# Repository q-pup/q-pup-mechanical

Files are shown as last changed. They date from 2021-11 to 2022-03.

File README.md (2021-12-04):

# q-pup-mechanical
CAD Models and Mechanical Design Calculations for Q-PUP

## McMaster-Carr Part Links
### Motor Module
- Cycloidal disk bearing: https://www.mcmaster.com/5972K341/ (x2)
- Cycloidal drive input/output bearing: https://www.mcmaster.com/5972K91/ (x2)
- Cycloidal drive pin bushings: https://www.mcmaster.com/6294K444/ (x8)
- Output hub bearing: https://www.mcmaster.com/5972K248/ (x1)

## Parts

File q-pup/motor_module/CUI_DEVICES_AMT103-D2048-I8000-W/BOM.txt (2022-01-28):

3DX_CUI_DEVICES_Supplier: CUI Devices
3DX_CUI_DEVICES_Description: AMT10 Axial, Adjustable Resolution, 2048 PPR, Single Index Pulse, 8 mm Bore, Wide, Incremental, Capacitive Modular Encoder
3DX_CUI_DEVICES_Model Number: AMT103-D2048-I8000-W

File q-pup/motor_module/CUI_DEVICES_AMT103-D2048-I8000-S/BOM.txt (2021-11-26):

3DX_CUI_DEVICES_Supplier: CUI Devices
3DX_CUI_DEVICES_Description: AMT10 Axial, Adjustable Resolution, 2048 PPR, Single Index Pulse, 8 mm Bore, Standard, Incremental, Capacitive Modular Encoder
3DX_CUI_DEVICES_Model Number: AMT103-D2048-I8000-S

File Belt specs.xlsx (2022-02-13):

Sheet: Sheet1
 | power [kW] | speed [RPM] | Torque [Nm] | Pulley dia [mm] | Force [N] | Belt Width [mm] | Tensile Strength per belt width [N/mm]
Req | 0.42 | 30.00 | 133.33 | 160.00 | 1666.67 |  |  | 103.2258065
Omega HP | 5.00 | 2850.00 | 16.75 | 76.39 | 438.60 | 9.00 | 48.73
 | 0.10 | 10.00 | 95.49 | 81.49 | 2343.55 | 20.00 | 117.18
 | 0.19 | 20.00 | 90.71 | 81.49 | 2226.37 | 20.00 | 111.32 | 1.328012435
 | 0.28 | 30.00 | 90.18 | 81.49 | 2213.35 | 20.00 | 110.67
 | 0.47 | 50.00 | 89.76 | 81.49 | 2202.94 | 20.00 | 110.15
 | 1.71 | 200.00 | 81.64 | 81.49 | 2003.74 | 20.00 | 100.19
 | 20.00 | 3000.00 | 63.66 | 81.49 | 1562.37 | 20.00 | 78.12
 | 43.92 | 8000.00 | 52.42 | 81.49 | 1286.61 | 20.00 | 64.33
DELTA | 0.22 | 20.00 | 105.04 | 81.49 | 2577.91 | 12.00 | 214.83
 | 0.32 | 30.00 | 100.26 | 81.49 | 2460.73 | 12.00 | 205.06 | 4101.214873 | 1.842105263
 | 0.41 | 40.00 | 97.88 | 81.49 | 2402.14 | 12.00 | 200.18

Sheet: Pulley Design
 | Name | URL | Pages |  |  |  | Source
[1] | Gates Powergrip Drive Design Manual | https://www.gates.com/content/dam/gates/home/knowledge-center/resource-library/catalogs/powergripdrivedesignmanual_17195_2014.pdf | 131, 138 | Teeth | 39 | 63
[2] | Technical Data Sheet - optibelt OMEGA HP 8M | https://www.optibelt.com/fileadmin/pdf/datenblaetter/Technical-Data-Sheet-optibelt-OMEGA-HP-8M.pdf | 1 | Pitch Dia | 99.31 | 160.43 | [3] | 56 | 5.614 | 5.560
[3] | Optibelt-TM-Rubber-Timing-Belt-Drives | https://www.optibelt.com/fileadmin/pdf/produkte/zahnriemen-gummi/Optibelt-TM-Rubber-Timing-Belt-Drives.pdf | 75 | Outside Dia | 97.94 | 159.06 | [3] | 63 | 6.316 | 6.262 | 160.42 | 159.05
 |  |  |  | Pitch Dia (Alt) | 99.31 | 160.42 | [1] | 64 | 6.416 | 6.362
 |  |  |  | Outside Dia (Alt) | 97.94 | 159.05 | [1]

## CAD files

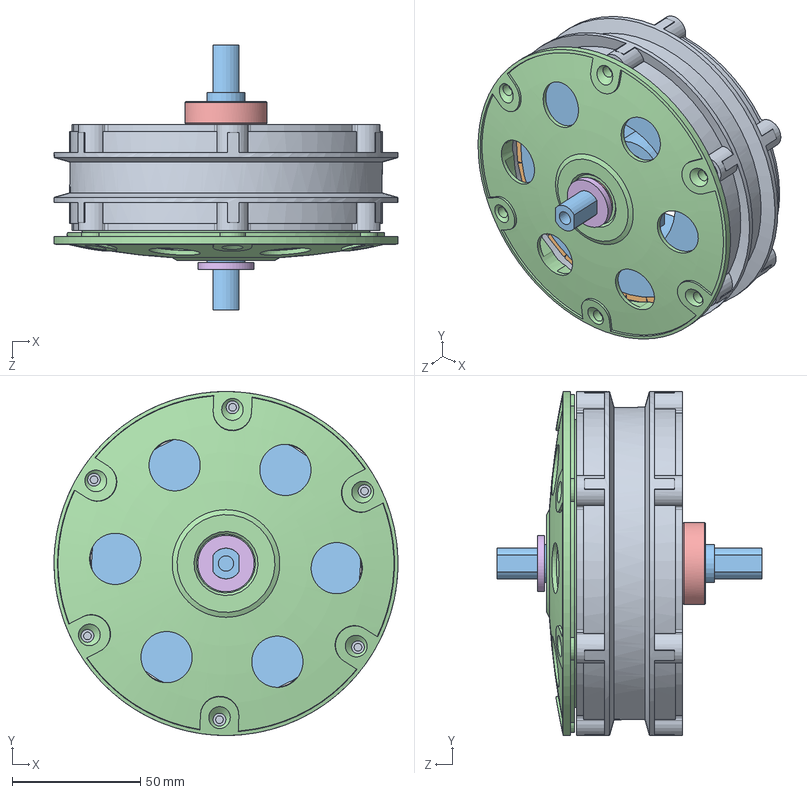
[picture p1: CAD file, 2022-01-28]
M365/M365.SLDASM
134.2 x 134.2 x 103.5 mm
M365 Rotor
M365 Magnet x 30
M365 Stator
M365 Cap
5972K83_Ball Bearing x 2
M365 Washer

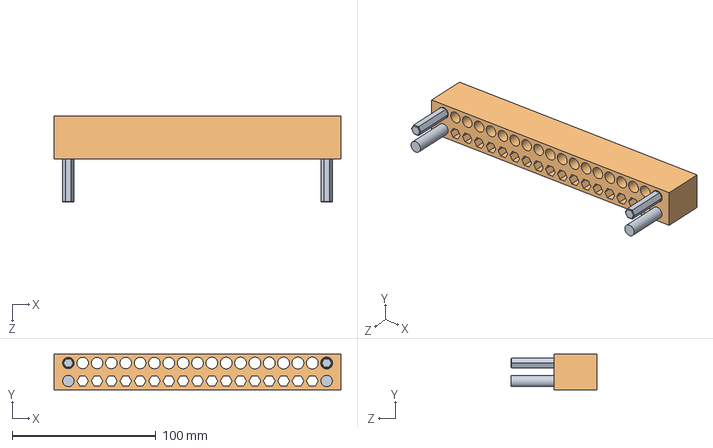
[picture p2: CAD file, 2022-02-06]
test-rigs/hex-circle-tolerance-test/hex-circle-tolerance-test.SLDASM
200.0 x 25.0 x 60.0 mm
pin x 4
Block

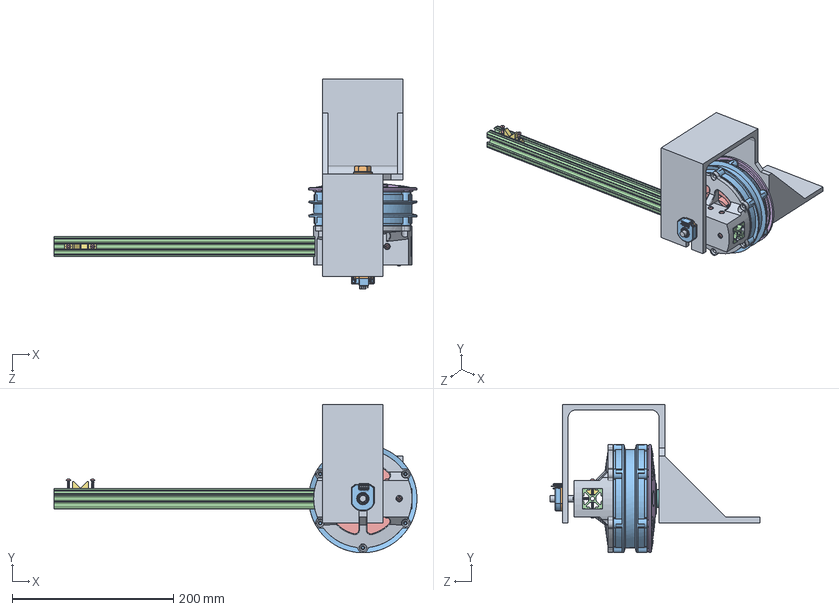
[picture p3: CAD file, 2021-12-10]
torque-test/torque_test.SLDASM
450.1 x 184.1 x 260.4 mm
test_stand
M365 Nut
M365 Rotor
M365 Magnet x 30
M365 Stator
M365 Cap
5972K83_Ball Bearing x 2
M365 Washer
torque_test_rotor_output
rotor_output_ring
CUI_DEVICES_AMT-Sleeve-REV-D(8 mm)
CUI_DEVICES_AMT-Hub-Top-REV-D1
CUI_DEVICES_AMT-Hub-Bottom-REV-B
CUI_DEVICES_AMT10X-Shaft-Adaptor-REV-E
CUI_DEVICES_Receiver-board
CUI_DEVICES_Rotor-board-REV F
CUI_DEVICES_Transmitter-board AMT10(AMT-103)
CUI_DEVICES_AMT-103-Base-REV-K(Default)
CUI_DEVICES_AMT-103-Top-Cover-REV-I
1010_17_48_CL
92095A472_Button Head Hex Drive Screw x 14
94459A140_Brass Heat-Set Inserts for Plastic x 14
rope_holder

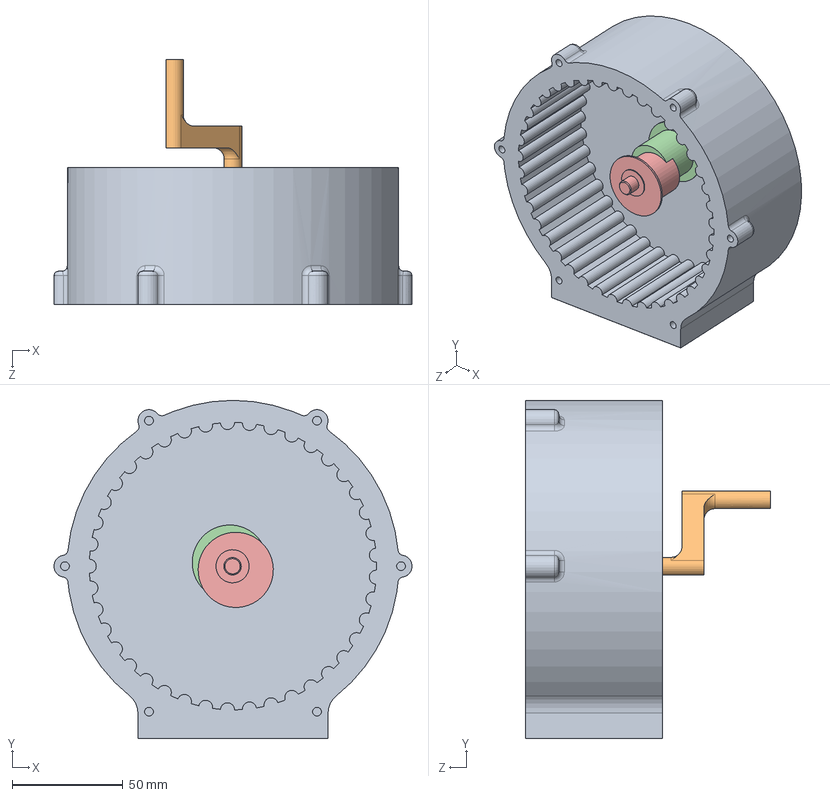
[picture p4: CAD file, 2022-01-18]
test-rigs/gearbox-test/sparse_gearbox.SLDASM
161.9 x 153.0 x 110.7 mm
gear_casing
central_crank_shaft
5972K91_Ball Bearing
cam_a
cam_b

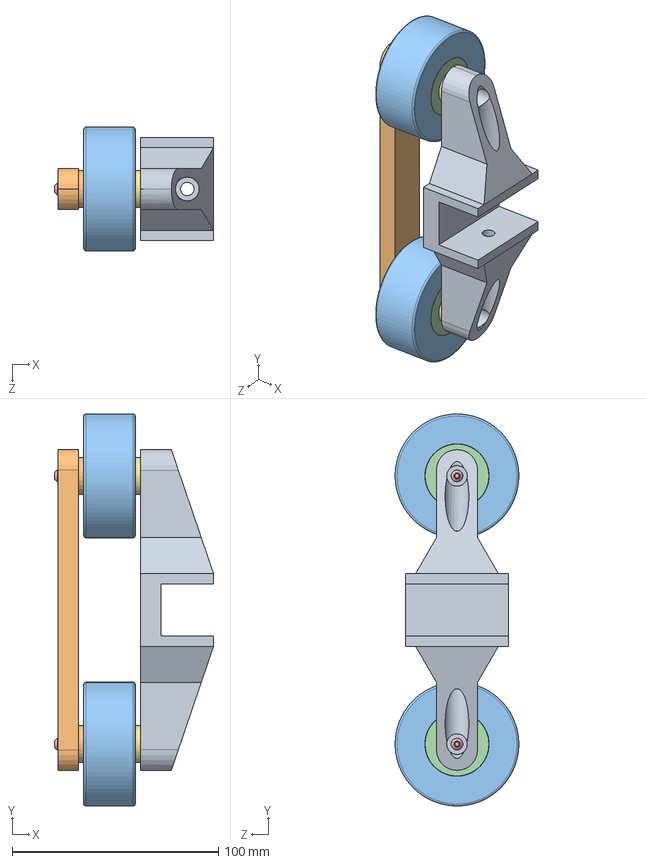
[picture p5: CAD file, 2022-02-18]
q-pup/belt_tensioner/belt_tensioner.SLDASM
77.1 x 190.0 x 59.9 mm
belt_tensioner_bracket
joiner
idler x 2
am-2986 FR8ZZ Hex Bearing.step x 4
92095A473_Button Head Hex Drive Screw x 4
94459A140_Brass Heat-Set Inserts for Plastic x 4
tensioner_washer x 2
hex_post x 2

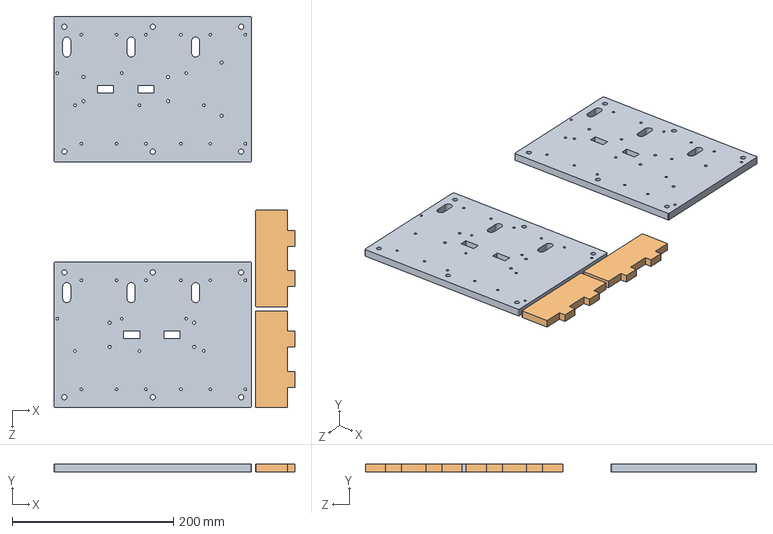
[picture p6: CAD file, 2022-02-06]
q-pup/chassis/3d-prints/odrive_panel_waterjet.SLDASM
299.0 x 9.53 x 485.5 mm
odrive_bracket x 2
bus_bar_divider x 2

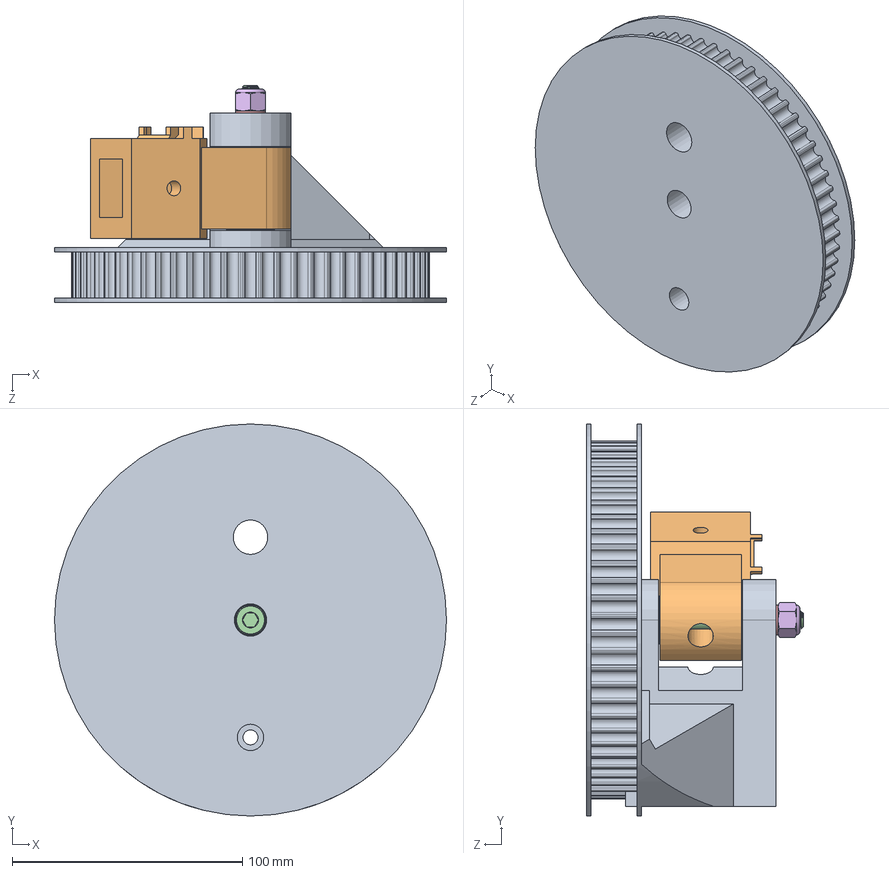
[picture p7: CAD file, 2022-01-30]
q-pup/knee_joint/knee_joint.SLDASM
170.4 x 170.4 x 94.5 mm
knee_lower_bracket
knee_upper_bracket
5972K91_Ball Bearing x 2
91290A460_Black-Oxide Alloy Steel Socket Head Screw
knee_spacer
93625A114_18-8 Stainless Steel Nylon-Insert Locknut

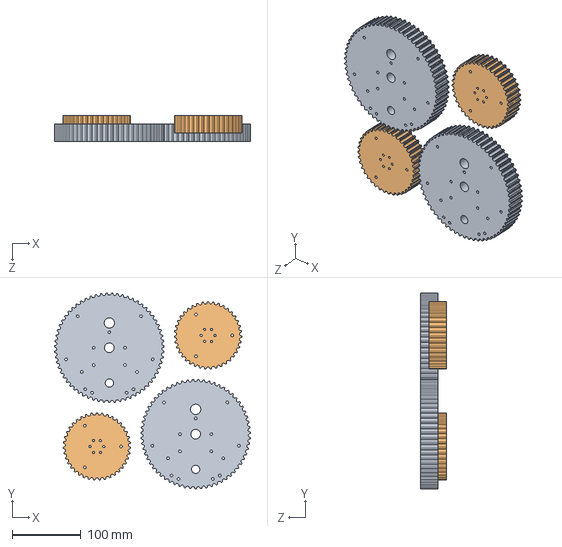
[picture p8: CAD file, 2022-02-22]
q-pup/leg/3d-prints/pulleys.SLDASM
284.2 x 284.2 x 38.1 mm
knee_pulley x 2
pulley x 2

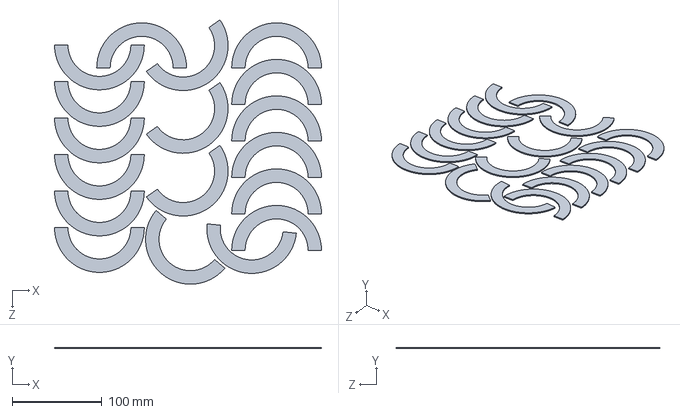
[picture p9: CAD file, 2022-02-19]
q-pup/leg/3d-prints/ptfe_bearings.SLDASM
297.2 x 1.59 x 294.2 mm
ptfe_bearing x 18

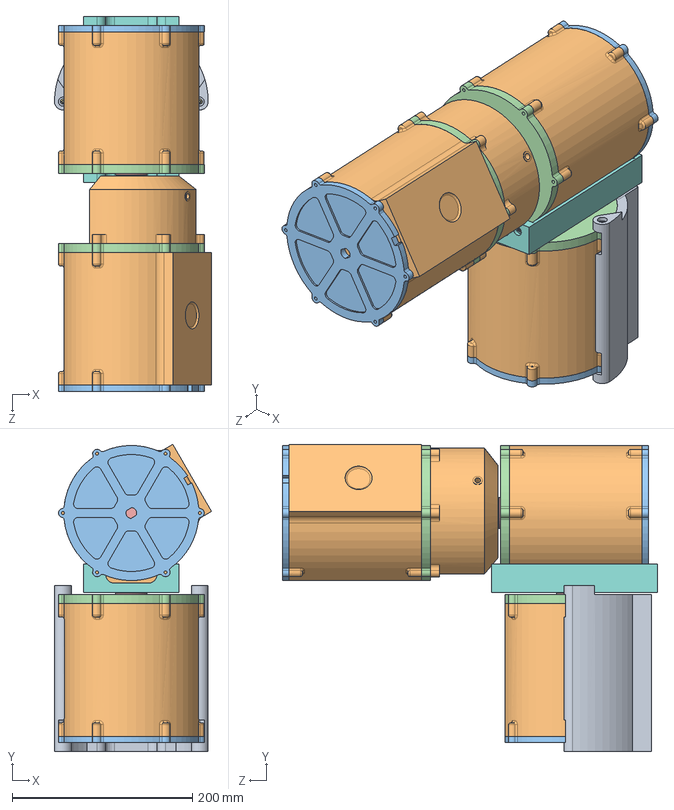
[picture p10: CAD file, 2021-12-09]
q-pup/leg/leg.SLDASM
174.4 x 341.2 x 416.4 mm
splay_motor_bracket
motor_casing x 3
motor_cap x 3
gearbox_cap x 3
output_shaft x 3
5972K365_Ball Bearing x 3
92095A473_Button Head Hex Drive Screw x 14
hip_motor_bracket
92095A472_Button Head Hex Drive Screw x 10
knee_motor_bracket

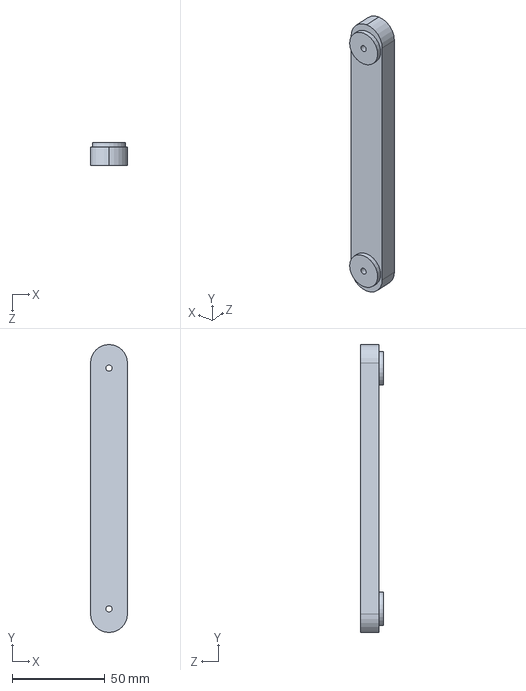
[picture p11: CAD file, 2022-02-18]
q-pup/belt_tensioner/joiner.SLDPRT
20.0 x 155.5 x 12.5 mm

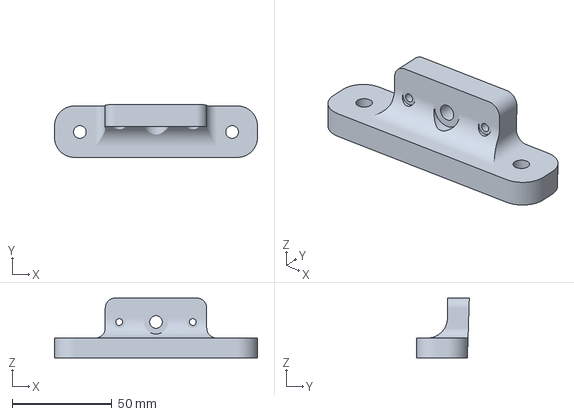
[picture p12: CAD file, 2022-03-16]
q-pup/chassis/3d-prints/CE3PRO_zed_bracket.3mf
101.6 x 26.4 x 30.0 mm

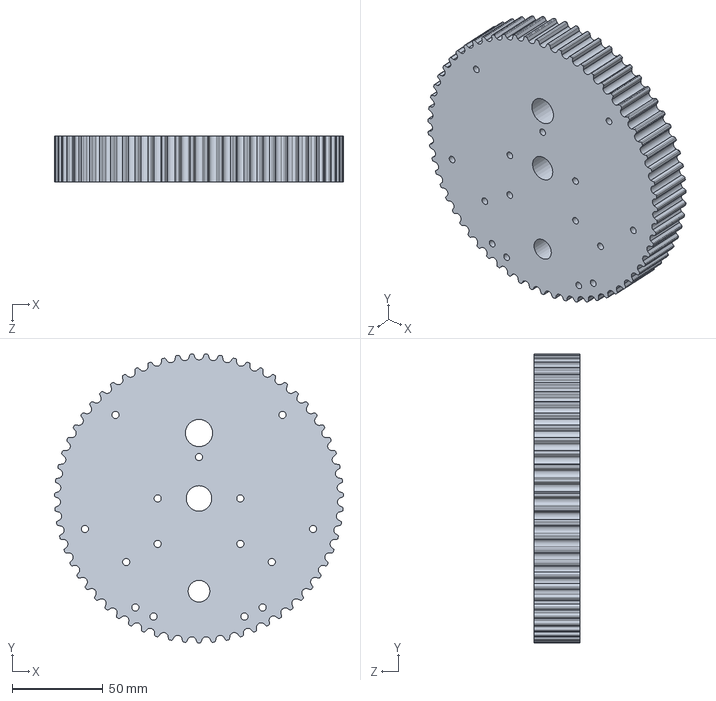
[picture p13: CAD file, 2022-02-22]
q-pup/knee_joint/knee_pulley.SLDPRT
159.0 x 159.0 x 25.4 mm

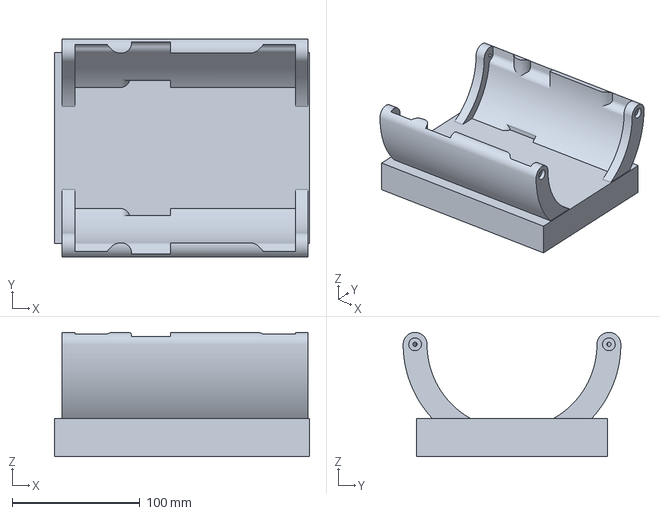
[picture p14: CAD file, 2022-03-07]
q-pup/leg/3d-prints/CE3PRO_hip_motor_bracket.3mf
200.0 x 170.7 x 97.4 mm

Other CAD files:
q-pup/motor_module/CUI_DEVICES_AMT103-D2048-I8000-S/CUI_DEVICES_CUI_DEVICES_AMT103-D0048-I8000-S.sldasm
q-pup/motor_module/CUI_DEVICES_AMT103-D2048-I8000-W/CUI_DEVICES_CUI_DEVICES_AMT103-D0048-I8000-W.sldasm
q-pup/belt_tensioner/3d-prints/idler_crowned.STL
q-pup/chassis/zed_bracket.SLDPRT
M365/5972K83_Ball Bearing.SLDPRT
M365/96194A104_Medium-Strength Steel Serrated Flange Locknut.SLDPRT
M365/M365 Cap.SLDPRT
M365/M365 Magnet.SLDPRT
M365/M365 Nut.SLDPRT
M365/M365 Rotor.SLDPRT
M365/M365 Stator.SLDPRT
M365/M365 Washer.SLDPRT
common/5972K91_Ball Bearing.SLDPRT
common/M2.5_fasteners/92095A459_Button Head Hex Drive Screw.SLDPRT
common/M2.5_fasteners/94459A439_Heat-Set Inserts for Plastic.SLDPRT
common/M3_fasteners/92095A472_Button Head Hex Drive Screw.SLDPRT
common/M3_fasteners/92095A473_Button Head Hex Drive Screw.SLDPRT
common/M3_fasteners/94459A140_Brass Heat-Set Inserts for Plastic.SLDPRT
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

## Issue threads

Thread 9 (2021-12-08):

Add dimension for printing tolerance of cycloidal disks

wmmc88, 2021-12-08:

Closed 2021-12-08.

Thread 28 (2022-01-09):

Consider set screw for shaft into rotor adaptor plate

matthew-reynolds, 2022-01-09:
> mild concern about the shaft deforming over time and introducing extra slop over time

Agreed, we could maybe put a set-screw into the rotor adaptor plate and an allen-key-sized hole in the motor casing? Or perhaps we should just see how it is for now.

_Originally posted by @matthew-reynolds in https://github.com/q-pup/q-pup-mechanical/issues/24#issuecomment-1008352812_

wmmc88, 2022-01-10:
I think for now just keep it as is, but keep it on our watchlist of stuff that may need iteration

matthew-reynolds, 2022-01-26:
Based on how the hex shaft was fitting in the torque test rotor adaptor, I'm going to close this for now. It can be re-opened if needed later.

Closed 2022-01-26.

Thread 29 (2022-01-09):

Crowned backside idlers

matthew-reynolds, 2022-01-09:
> > Dunno if the idlers should be crowned or not. I suspect probably yes, but currently they are drawn flat. Advantage to crowning is centering the belt, disadvantage is slightly harder to print and slightly more belt wear. We'll probably have to make then crowned in a follow-up.
>
> crowned sounds good

ok. Will do in follow up.

_Originally posted by @matthew-reynolds in https://github.com/q-pup/q-pup-mechanical/issues/25#issuecomment-1008353152_

matthew-reynolds, 2022-01-19:
didn't do this yet because I'm a bit worried about belt wear. I think we should see how it runs without crowning first.

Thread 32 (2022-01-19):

Increase Fillet Radius for Motor Module End Screws

wmmc88, 2022-01-19:
Its a tad droopy right now because I refuse to waste filament to support it. A larger more gradual fillet would probably fix it.

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

matthew-reynolds, 2022-01-21:
Closed in #49

Closed 2022-01-21.

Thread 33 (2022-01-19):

Retolerance motor module parts to new spec

wmmc88, 2022-01-19:
Set tolerances to some number between 0.075 and 0.1mm

Using the [v2 makers muse tolerance guage](https://www.makersmuse.com/clearance-and-tolerance-3d-printer-gauge)

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

wraftus, 2022-01-20:
## Features with tolerance
- [ ] hex bore in [`rotor_adapter`](https://github.com/q-pup/q-pup-mechanical/blob/main/q-pup/motor_module/rotor_adaptor.SLDPRT)
- [ ] hex bore in [`cam_a`](https://github.com/q-pup/q-pup-mechanical/blob/main/q-pup/motor_module/cam_a.SLDPRT)
- [ ] hex bore in [`cam_b`](https://github.com/q-pup/q-pup-mechanical/blob/main/q-pup/motor_module/cam_b.SLDPRT)
- [ ] bearing bore and pitch radius in [`cycloidal_disk`](https://github.com/q-pup/q-pup-mechanical/blob/main/q-pup/motor_module/cycloidal_disk.SLDPRT)
- [ ]  bearing bore in [`motor_casing`](https://github.com/q-pup/q-pup-mechanical/blob/main/q-pup/motor_module/motor_casing.SLDPRT)
- [ ] pin bore and in [`output_shaft`](https://github.com/q-pup/q-pup-mechanical/blob/main/q-pup/motor_module/output_shaft.SLDPRT)
- [ ] ??? in [`rotor_adapter_ring`](https://github.com/q-pup/q-pup-mechanical/blob/main/q-pup/motor_module/rotor_adaptor_ring.SLDPRT)

matthew-reynolds, 2022-01-20:
We shouldn't need a list of things, if you just update the tolerances file everything will update

wmmc88, 2022-01-20:
I think @wraftus mightve wanted to do a sanity check that those things are all toleranced

Closed 2022-02-06.

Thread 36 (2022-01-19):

Add Larger Chamfers/Fillets on holes that are on Print bed surfaces

wmmc88, 2022-01-19:
Unless I waste filament and print time on a raft or painstakingly level each time (much pain, very slow), the holes on the bottom can somtimes be a tiiiiinny bit squished. Larger chamfers or fillets would avoid this.

matthew-reynolds, 2022-01-20:
wdym squished? Like undersized?

Which parts have you run into this with so far? Breaking that corner doesn't always sound possible

wmmc88, 2022-01-20:
> wdym squished? Like undersized?
>
> Which parts have you run into this with so far? Breaking that corner doesn't always sound possible

Cam A hex is the one off the top of my head but I've run into it b4. It's just occasionally the bed might not be perfectly level so the filament on the first layer gets a lil squished cuz it's printing too close

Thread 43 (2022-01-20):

Make gearbox easier to assemble

wraftus, 2022-01-20:
- [ ] notches to align cam with cycloidal gear
- [ ] ... add after assembly

matthew-reynolds, 2022-01-20:
wdym align cam with cycloidal gear? There's a bearing between them, right?

matthew-reynolds, 2022-01-23:
@wraftus Assigned myself, I'll do this with the visual features we mentioned

Closed 2022-01-23.

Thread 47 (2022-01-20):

Design leg testing fixture

wraftus, 2022-01-20:

Closed 2022-02-06.

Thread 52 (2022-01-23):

Tolerance hex in rotor adapter plate

matthew-reynolds, 2022-01-23:
Both torque test and real versions

Closed 2022-01-23.

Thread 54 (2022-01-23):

Fix torque test assy

matthew-reynolds, 2022-01-23:

Closed 2022-01-23.

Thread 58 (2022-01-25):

Hex Test Fit Part

wmmc88, 2022-01-25:
A simple test part to verify printing tolerances for hex shaft in hex hole

Closed 2022-02-06.

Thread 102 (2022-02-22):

Fix knee motor bracket extra hole

matthew-reynolds, 2022-02-22:

Closed 2022-02-23.

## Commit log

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2021-11-26 CAD: Add prelim M365 model
    [M365 Cap.SLDPRT, M365 Magnet.SLDPRT, M365 Rotor.SLDPRT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]
2021-11-26 CAD: Add 2D gait angles sketch
    [GaitAngles.SLDPRT]
2021-11-26 CAD: Update shaft diameter
    [M365 Cap.SLDPRT, M365 Stator.SLDPRT, M365.SLDASM]
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2021-11-26 Move rough sketches to 'sketches' dir
    [DogGeometry.SLDPRT, GaitAngles.SLDPRT]
2021-11-26 Create motor module assy; Add motor output shaft
    [M365.SLDASM, motor_module.SLDASM, rotor_output.SLDPRT]
2021-11-26 Update M365 motor cap to be structurally viable
    [M365 Cap.SLDPRT, M365.SLDASM]
2021-11-26 Draw first pass of motor module
    Missing the gearbox; This is just the motor + encoder assy
    [5972K248_Ball Bearing.SLDPRT, 5972K91_Ball Bearing.SLDPRT, CUI_DEVICES_AMT-103-Base-REV-K(Default).sldprt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]
2021-11-26 Add fasteners for motor casing
    [92095A472_Button Head Hex Drive Screw.SLDPRT, 94459A140_Brass Heat-Set Inserts for Plastic.SLDPRT, M365.SLDASM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]
2021-11-26 Add filets and weight reduction
    [M365.SLDASM]
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2021-11-26 Add prelim gearbox output
    Additionally:
    - Complete the casing
    - Rotate hex pattern by 30deg
    - Add channel for encoder wires
    [M365.SLDASM, gearbox_cap.SLDPRT, motor_cap.SLDPRT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]
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2021-11-26 Fix rotor shaft length
    [M365.SLDASM, rotor_output.SLDPRT]
2021-11-27 Flip cam flanges to properly constrain the bearings
    [cam_a.SLDPRT, cam_b.SLDPRT]
2021-11-27 Add output shaft bearing
    This axially constrains the cycloidal gearbox components, and
    provides support to the output shaft
    [M365.SLDASM, cam_a.SLDPRT, cam_b.SLDPRT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]
2021-11-27 Add base to motor module
    Additionally, increase encoder cable channel depth
    [M365.SLDASM, motor_cap.SLDPRT, motor_casing.SLDPRT]
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2021-12-03 Mark fasteners as IsFastener=1
    This property helps sort parts in interference detection
    [92095A472_Button Head Hex Drive Screw.SLDPRT, 94459A140_Brass Heat-Set Inserts for Plastic.SLDPRT]
2021-12-03 Resolve precision issues
    Solidworks rounds things. Since our eccentricity is rational, it was
    getting rounded, and the rounding stack-up was breaking things. So I
    re-defined a couple dims in the cycloidal disc sketch to avoid error
    stackup. I also explicitly rounded the value to 0.01mm to avoid
    different documents w/ different precisions from making a mess.
    I also fully defined the assembly, and checked collision of the
    cycloidal discs and pins.
    [M365.SLDASM, cam_a.SLDPRT, cam_b.SLDPRT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]
2021-12-03 Set materials and add light motor_module config
    Currently, PETG for all 3D printed parts. Random metals for COTS parts.
    (I used 1060 for the motor's rotor and cap, and bronze for the stator
    and magnets, since there weren't neodyniam alloys and the colour is nice
    lol)
    [M365 Cap.SLDPRT, M365 Magnet.SLDPRT, M365 Rotor.SLDPRT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]
2021-12-03 Counter-bore bushings into output shaft
    Resolves final interference in the assembly.
    [M365.SLDASM, cam_a.SLDPRT, cam_b.SLDPRT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]
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2021-12-03 Fix some undersized parts
    [cam_a.SLDPRT, cam_b.SLDPRT, cycloidal_disk.SLDPRT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]
2021-12-03 Revert cam back to the original configuration, Walter was wrong
    [cam_a.SLDPRT, cam_b.SLDPRT, cycloidal_disk.SLDPRT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]
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2021-12-08 Update motor module & rotor output adapter
    Dimensions match real motor.
    [M365 Cap.SLDPRT, M365 Nut.SLDPRT, M365.SLDASM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]
2021-12-08 Replace 6907 output bearing w/ 6007.
    Slightly larger, but substantial cost savings. Lengthens module by 4mm.
    Also chamfered all bearing ODs to make installation easier.
    [5972K248_Ball Bearing.SLDPRT, 5972K365_Ball Bearing.SLDPRT, M365.SLDASM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]
2021-12-08 Add cycloidal disc clearance tolerance param
    [M365.SLDASM, cam_a.SLDPRT, cam_b.SLDPRT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]
2021-12-08 Add no-cycloidal-bushing configuration
    Also add lots of bearing chamfers to facilitate installation
    [M365.SLDASM, cam_a.SLDPRT, cam_b.SLDPRT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]
2021-12-09 Create rough torque test fixture
    [rotor_output.SLDPRT, torque_test.SLDASM]
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2021-12-09 Add hip, knee, and splay motor brackets
    Additionally, add indent to bottom of motor module
    to accomodate bolt heads
    [92095A473_Button Head Hex Drive Screw.SLDPRT, M365.SLDASM, cam_a.SLDPRT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]
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2021-12-09 Add knee joint, leg bones, and fasteners to leg
    [1010_12_56_CL.sldprt, 1010_17_48_CL.sldprt, 3205.sldprt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]
2021-12-09 Fix naming
    [M365.SLDASM, torque_test.SLDASM]
2021-12-09 Revert M365.SLDASM changes
    Stupid Solidworks
    [M365.SLDASM]
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2021-12-09 Redesign toque test fixture
    [test_stand.SLDPRT, torque_test.SLDASM]
2021-12-09 Add back one side of encoder support arm
    [test_stand.SLDPRT, torque_test.SLDASM]
2021-12-09 Use set-screws to hold 8020 in place.
    Also, add slot to facilitate assembly.
    [3205.sldprt, 92949A267_18-8 Stainless Steel Button Head Hex Drive Screw.SLDPRT, M365.SLDASM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]
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2021-12-10 Add bracket to locate rope on lever arm
    [1010_17_48_CL.sldprt, rope_holder.SLDPRT, torque_test.SLDASM]
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2021-12-10 Replace chamfer with fillet
    [M365.SLDASM, torque_test_rotor_output.SLDPRT]
2021-12-14 add 3d printer files used for initial torque tests
    [FFpp_rotor_output_ring+rope holder.g, rope_holder.STL, rotor_output_ring.3mf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]
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2021-12-23 Tolerance motor module
    [M365.SLDASM, cam_a.SLDPRT, cam_b.SLDPRT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]
2021-12-23 Reduce tolerances by half
    [M365.SLDASM, cam_a.SLDPRT, cam_b.SLDPRT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]
2021-12-23 Fix magnet size
    [M365 Magnet.SLDPRT, M365.SLDASM]
2021-12-23 Add offset cycloidal disc config
    The two discs should be asymmetrical. The gearbox now meshes correctly.
    [M365.SLDASM, cam_a.SLDPRT, cam_b.SLDPRT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]
2021-12-23 Tolerance knee joint
    [knee_joint.SLDASM, knee_lower_bracket.SLDPRT, knee_spacer.SLDPRT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]
2021-12-23 Tolerance motor brackets & leg assy
    [M365.SLDASM, cam_a.SLDPRT, cam_b.SLDPRT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]
2021-12-23 Add corner rad tolerance to motor module casing
    [motor_casing.SLDPRT]
2021-12-24 Replace output plate shaft with removable shaft
    Also, correct tolerance stackup on rotor adaptor ring & groove
    [M365.SLDASM, cam_a.SLDPRT, cam_b.SLDPRT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]
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2022-01-06 Update leg assy with (SpeedPak'd) motor module.
    Since the motors are SpeedPak'd, the hip and splay remain inflexible for
    now
    [M365.SLDASM, belt_tensioner.SLDASM, belt_tensioner_bracket.SLDPRT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]
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2022-01-16 Fix lower leg angle in all leg configs
    [belt_tensioner.SLDASM, belt_tensioner_bracket.SLDPRT, bus_bar.SLDASM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]
2022-01-17 Fix knee belts in full assy
    [belt_tensioner.SLDASM, belt_tensioner_bracket.SLDPRT, hip_motor_bracket.SLDPRT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]
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2022-01-17 Update Jetson model & bracket
    Also, reduce assembly file sizes a bit.
    [belt_tensioner.SLDASM, belt_tensioner_bracket.SLDPRT, breaker_bracket.SLDPRT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]
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2022-01-18 Replace T-Slot fasteners in leg
    [47065T905_T-Slotted Framing.SLDPRT, 91255A539_Button Head Hex Drive Screw.SLDPRT, belt_tensioner.SLDASM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]
2022-01-18 Replace T-Slot fasteners in main assy
    [jetson_bracket.SLDPRT, knee_joint.SLDASM, knee_lower_bracket.SLDPRT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]
2022-01-19 Replace T-Slot fasteners in chassis
    [1010_24_8_CL.sldprt, 1010_9_84_CL.sldprt, 91255A542_Button Head Hex Drive Screw.SLDPRT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]
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2022-01-20 Make encoder shaft removeable and add 8020 tolerance in torque test
    [shaft.SLDPRT, torque_test_rotor_output.SLDPRT]
2022-01-20 Add tolerance to torque test 8020 slot
    [shaft.SLDPRT, torque_test_rotor_output.SLDPRT]
2022-01-20 Add tolerance to rotor ring groove and add eof newline
    [shaft.SLDPRT, torque_test_rotor_output.SLDPRT]
2022-01-20 Add radius to corners on rotor adaptor ring
    [rotor_adaptor_ring.SLDPRT]
2022-01-20 Increase fillet & chamfer on motor casing screw mount
    [belt_tensioner.SLDASM, belt_tensioner_bracket.SLDPRT, cam_a.SLDPRT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]
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2022-01-23 Add missing tols on torque test rotor adaptor
    Specifically, the bearing seat OD and groove OD
    [torque_test_rotor_output.SLDPRT]
2022-01-23 Tolerance all hex shafts & bores to tol_general_slip
    [cam_a.SLDPRT, cam_b.SLDPRT, central_crank_shaft.SLDPRT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]
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2022-01-23 Replace end-face bolt with new part
2022-01-23 Fix mates on hex shafts
    [M365.SLDASM, cam_a.SLDPRT, cam_b.SLDPRT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]
2022-01-23 add 3d print files for torque test v2
    [FFpp_rotor_adaptor_ring_0.6n_0.2mm.g, FFpp_rotor_output_ring+rope holder.g, FFpp_shaft_0.6n_0.2mm_L-PVA_R-PETG.g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]
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2022-01-25 updated rotor_adaptor_ring 3mf to use variable layer height
    [rotor_adaptor_ring.3mf]
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2022-01-27 Flip bolt alignment between motor & gearbox casings
    [M365.SLDASM, cam_a.SLDPRT, cam_b.SLDPRT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]
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2022-01-27 Reduce encoder cable clearance by 5mm
    [M365.SLDASM, cam_a.SLDPRT, cam_b.SLDPRT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]
2022-01-27 Replace AMT103 encoder & mount with wide-base
    Also fixed hole dias for joining the motor & gearbox casings
    [47065T905_T-Slotted Framing.SLDPRT, 91255A539_Button Head Hex Drive Screw.SLDPRT, 91255A542_Button Head Hex Drive Screw.SLDPRT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]
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2022-01-31 Add a fixture for testing a full leg
    [diagonal_beam.SLDPRT, diagonal_floor_beam.SLDPRT, floor_beam.SLDPRT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]
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2022-02-01 Split upper pulley into two pieces
    This should help with printing
    [pulley.SLDPRT, pulley_wall.SLDPRT]
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2022-02-02 updated tolerances
    [Block.3mf, Block.SLDPRT, Block.STL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]
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2022-02-05 Replace 3D printed odrive panel w/ PC
    [bus_bar_divider.SLDPRT, odrive_bracket.SLDPRT]
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2022-02-06 changed to use latest tolerances
    [output_shaft.3mf, output_shaft.STL]
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2022-02-09 Prepare front & rear battery brackets for printing
    [battery_bracket_front.STL, battery_bracket_rear.STL]
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2022-02-11 Crown idler, and make parts printable
    Slight redesign to remove overhangs
    [belt_tensioner.SLDASM, belt_tensioner_bracket.SLDPRT, idler.SLDPRT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]
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2022-02-12 Strengthen knee motor bracket
    [knee_motor_bracket.SLDPRT]
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2022-02-13 update motor cap with flat bottom. fit 2 prints on single bed
    [motor_cap.3mf, motor_cap.STL]
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2022-02-13 fix dshaft reinforcement on motor cap
    [motor_cap.3mf]
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2022-02-18 Add 608 bearing test version of output shaft
    [output_shaft.SLDPRT]
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2022-02-19 knee upper bracket reinforcemtn
    [knee_upper_bracket.3mf]
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2022-02-20 update for reinforced knee motor bracket
    [knee_motor_bracket.STL]
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2022-02-20 Fix knee spacer STL
    [knee_spacer.STL]
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2022-02-20 Reinforce lower knee bracket
    - Make chamfer taller
    - Widen bolt head holes for 1/4-20s
    [knee_lower_bracket.SLDPRT, knee_pulley.SLDPRT]
2022-02-21 prevent extruder crash
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2022-02-22 Add "Waterjet" pulley configs & fix hole dias
    [knee_pulley.SLDPRT, pulley.SLDPRT, pulleys.DWG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]
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2022-02-22 Fix 1/4-20 bolt hole
    [knee_motor_bracket.SLDPRT]
2022-02-23 Update Jetson bracket
    - Provides more printable
    - More printable
    - Easier to get on/off chassis
    [jetson_bracket.SLDPRT, jetson_spacer.SLDPRT]
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2022-02-24 Increase pin aligner height from 7 to 17mm
    [pin_aligner.SLDPRT, pin_aligner_no_bearings.STL]
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2022-02-24 Add aligning features on gearbox cap & casing
    [gearbox_cap.SLDPRT, gearbox_casing.SLDPRT]
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2022-02-27 Reinforce hip motor bracket
    TODO: Increase walls slightly more to get rid of infill?
    TODO: Increase priming slightly?
    [CE3PRO_hip_motor_bracket.3mf]
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2022-03-05 Gearbox casing print
    Casing with groove, from #112
    [gearbox_casing.STL]
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2022-03-05 sketchy stiched together gcode for dual head duplicate print of central shaft
    [central_shaft.3mf]
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2022-03-05 update z layer for custom stitched disk gcode
    [MODIFIED_cycloidal_disk_a_40_0.02.3mf, MODIFIED_cycloidal_disk_ab_40_0.02.3mf, MODIFIED_cycloidal_disk_b_40_0.02.3mf]
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2022-03-05 several central shaft tolerances
    [FFpp_CUSTOM_central_shaft+0.0625.g, FFpp_CUSTOM_central_shaft+0.075.g, FFpp_CUSTOM_central_shaft.g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]
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
